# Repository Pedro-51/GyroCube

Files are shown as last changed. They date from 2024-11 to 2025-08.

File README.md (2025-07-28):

# GyroCube
 Self Balancing Cube Project

Balancing Cube project based on the "remrc" model: https://www.thingiverse.com/thing:6695891

    Creation of an Application to facilitate calibration and motor testing,
    Merging the main program with the motors test program,
    Creation of a printed circuit for those who wish to have a beautiful object,
    Addition of a Power button,
    Addition of a button to turn on the LEDs and change their colors,
    Modified the face files for placing the switches in 12 and 16mm. Thanks to dinomight.

Explanatory video: https://youtu.be/zuOgj580Nhk<br>
Led function video: https://youtu.be/vczHyelNjr4<br>
PCB: https://www.pcbway.com/project/shareproject/GyroCube_v1_1_5d583cf0.html<br>
Android app: [French](Appli%20APK/Cube_1_01_fr.apk),[English](Appli%20APK/Cube_1_01_en.apk)<br>

#######################################################################################

For the program to work, you need to install esp32 by expressif v2.0.17 board version

#######################################################################################

## 12-5-2024 (Dinomight/Darkmadda)
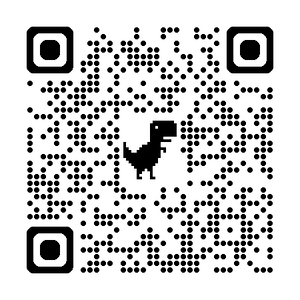
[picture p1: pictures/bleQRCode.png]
Added new [BLE firmware](esp32_cube_vBLE_en/) this has a browser based config tool (can be use on android/mac/pc via chrome). The firmware is written to be used with platformio rather than the arduino ide. it may still work the arduino ide but i'm not sure (Platformio is far superior anyways). This firmware is backwards compatible with other app config methods (Bluetooth Serial, Pedro android app). I however think the new BLE tool is superior. I'm a little biased but try it you'll see. no need to host the app i set it up on hosting that should never go away https://idoxa55.sufydely.com/cubeConfigTool.html.

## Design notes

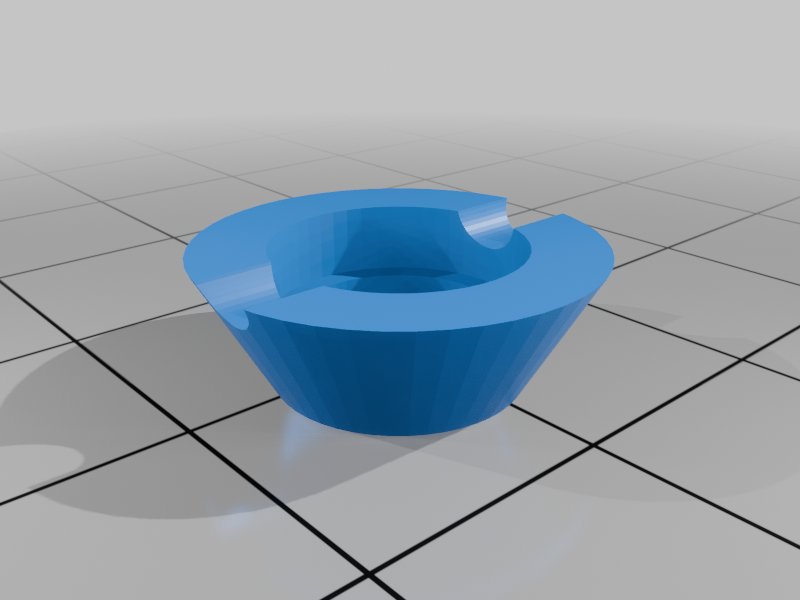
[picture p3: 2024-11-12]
3D_files/images/0f9c7aa1-d16f-406a-a5ba-5303668963a1.png

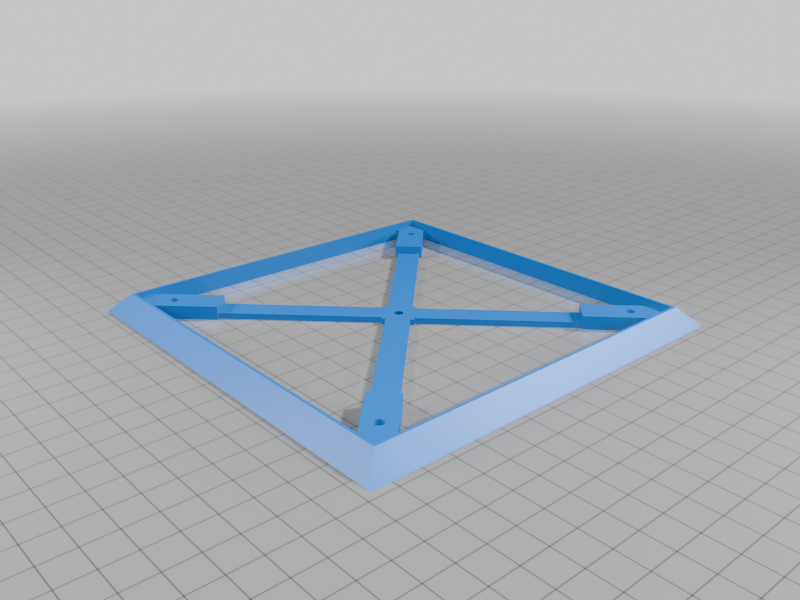
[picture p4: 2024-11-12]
3D_files/images/1357592c-b74b-4802-8180-4ac7882b1fb2.png

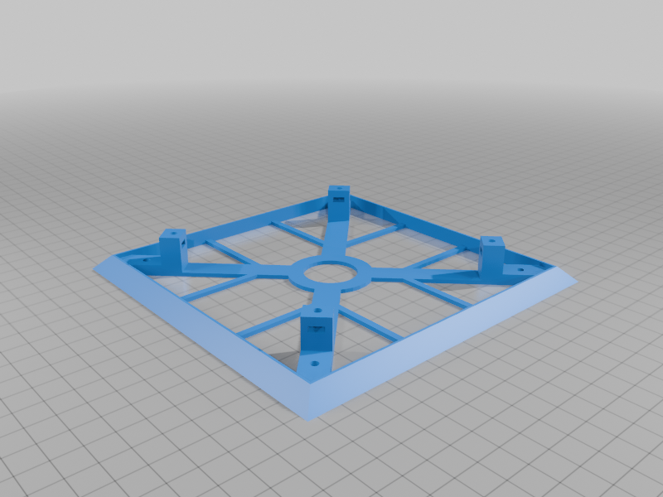
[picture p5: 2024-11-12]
3D_files/images/8a100be1-da8e-4f1d-b831-8e430dd452ee.png

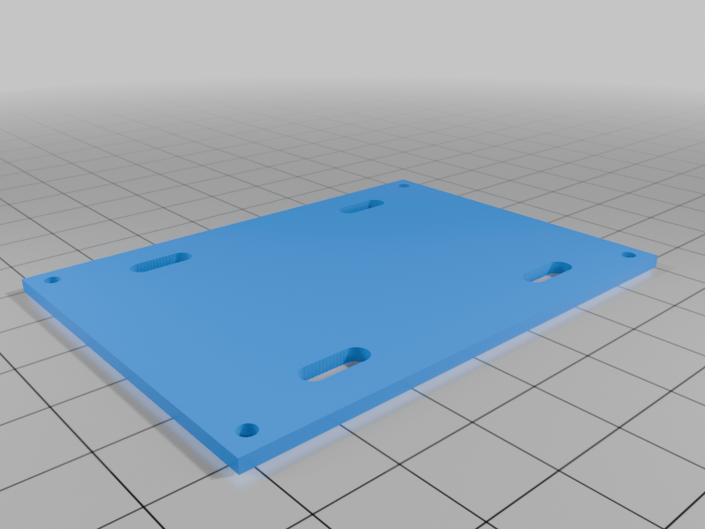
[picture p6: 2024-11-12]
3D_files/images/8ea0aab7-f794-4f8a-a906-e5200b60cf10.png

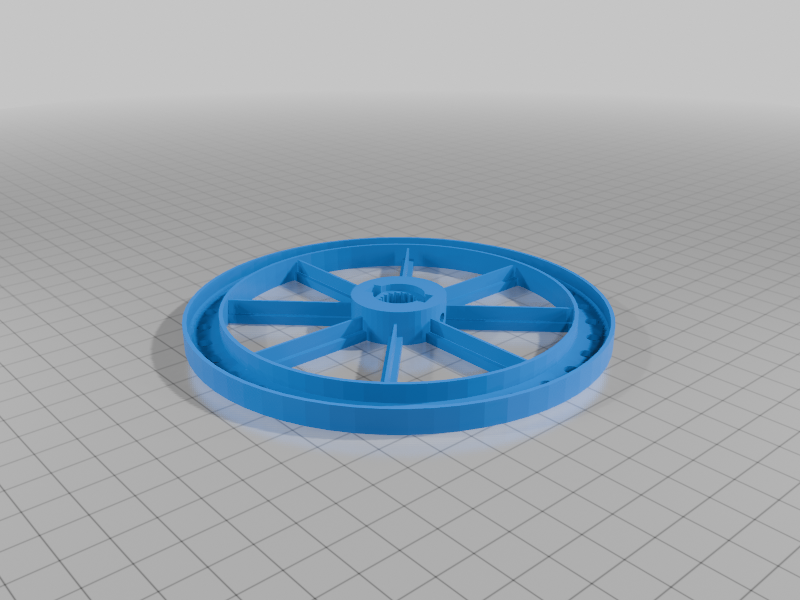
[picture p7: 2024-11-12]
3D_files/images/49ab8330-d06a-4846-8612-64cba1623243.png

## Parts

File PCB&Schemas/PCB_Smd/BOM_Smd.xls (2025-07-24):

Reference | Packages | Value | Qty | Comments
BT1 |  | Battery lipo 3s 650mah | 1
BZ1 |  | Buzzer 5v | 1
C1,C2 | 1206 SMD | 100nf | 2
J6,J7,J8 | JST-ZH 15cm | Connector jst-zh 01x08 double head | 3
J13 | JST-ZH 10cm | Connector jst-zh 01x03 with wire | 1
J12 | JST-ZH 10cm | Connector jst-zh 01x04 with wire | 1
Q1 | Sot-23-3 | MMBT2222A | 1
R1,R5 | 1206 SMD | 1k | 2
R2 | 1206 SMD | 33k | 1
R3,R4 | 1206 SMD | 10k | 2
SW1 | Ø16mm or Ø12mm 12-24v | Latch power inox switch | 1
SW2-1 | Ø16mm or Ø12mm 3-6v | Momentary inox switch | 1
SW2-2 |  | SMD switch reset Push | 1
U1 | mini360 | DC-DC 5v step down | 1
U2 | 30pin-micro module | esp32-wroom-32D cp2102 | 1
PCB | PCBway | PCB by Pedro51 | 1 | GyroCube_v1_2_Smd (https://www.pcbway.com/project/shareproject/GyroCube_v1_1_5d583cf0.html)
Wire | Silicon black wire | 16 AWG 100mm | 1
Wire | Silicon red wire | 16 AWG 100mm | 1
Wire | Silicon black wire | 24 AWG 100mm | 1
MPU6050 |  | Gyroscope | 1
WS1812 Led | Strip pcb for drone | Leds RGB PandaRC | 1
NIDEC 24H |  | Encoder Motor | 3
Battery Plug | Male | XT30 | 1
Screws | countersunk head screws | M4x8mm | 72
Screws | round head screw | M4x10mm | 12
Nuts | - | M4 | 144
Screws | countersunk head screws | M3x10mm | 36
Screws | countersunk head screws | M3x14mm | 12
Nuts | - | M3 | 52

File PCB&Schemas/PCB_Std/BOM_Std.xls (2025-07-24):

Reference | Packages | Value | Qty | Comments
BT1 |  | Battery lipo 3s 650mah | 1
BZ1 |  | Buzzer 5v | 1
C1,C2 | ceramic | 100nf-50v | 2
C3 | Polarized chimic | 100uf-10v | 1
J6,J7,J8 | JST-ZH 15cm | Connector jst-zh 01x08 double head | 3
J13 | JST-ZH 10cm | Connector jst-zh 01x03 with wire | 1
J12 | JST-ZH 10cm | Connector jst-zh 01x04 with wire | 1
Q1 | TO92 | 2n2222 | 1
R1,R5 | 1/4w | 1k | 2
R2 | 1/4w | 33k | 1
R3,R4 | 1/4w | 10k | 2
SW1 | Ø16mm or Ø12mm 12-24v | Latch power inox switch | 1
SW2-1 | Ø16mm or Ø12mm 3-6v | Momentary inox switch | 1
SW2-2 |  | switch reset Push | 1
U1 | TO220 | LM7805 DC-DC 5v regulator | 1
U2 | 30pin-micro module | esp32-wroom-32D cp2102 | 1
PCB | PCBway | PCB by Pedro51 | 1 | GyroCube_v1_2_Std (https://www.pcbway.com/project/shareproject/GyroCube_v1_2_Smd_9171484b.html)
Wire | Silicon black wire | 16 AWG 100mm | 1
Wire | Silicon red wire | 16 AWG 100mm | 1
Wire | Silicon black wire | 24 AWG 100mm | 1
MPU6050 |  | Gyroscope | 1
WS1812 Led | Strip pcb for drone | Leds RGB PandaRC | 1
NIDEC 24H |  | Encoder Motor | 3
Battery Plug | Male | XT30 | 1
Screws | countersunk head screws | M4x8mm | 72
Screws | round head screw | M4x10mm | 12
Nuts | - | M4 | 144
Screws | countersunk head screws | M3x10mm | 36
Screws | countersunk head screws | M3x14mm | 12
Nuts | - | M3 | 52

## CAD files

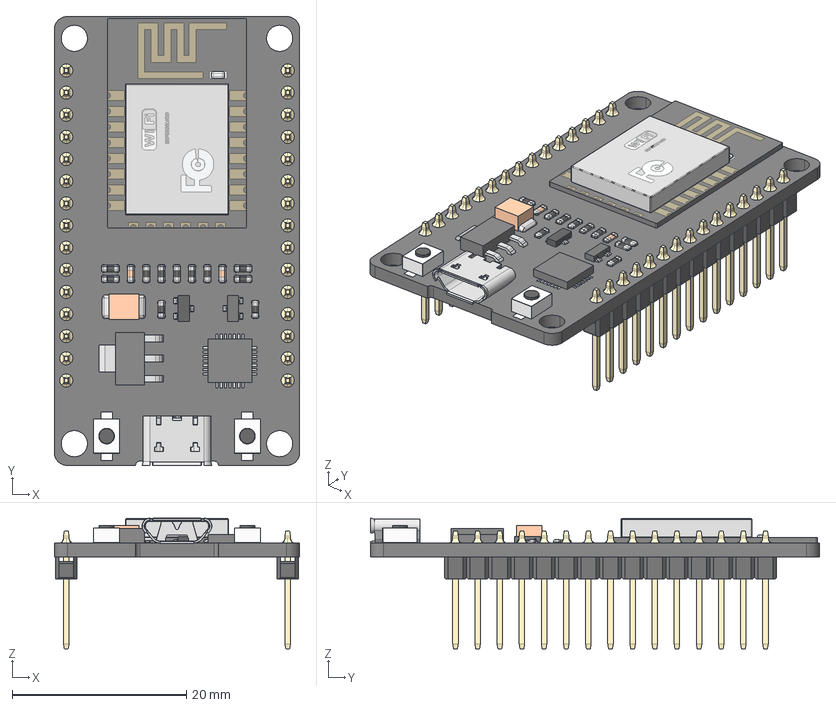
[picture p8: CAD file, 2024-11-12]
PCB&Schemas/PCB_Smd/Kidad_PCB_Smd/3d_Model/esp32_dev_kit_v1_asm.stp
28.1 x 51.5 x 15.0 mm
PCB
PIN x 30
WIFI_CARD_2
RECTANGULARCHIP_2
MICROCHIP_2
TANCHIP_2
TRANSISTOR_3-LEG_2
RESISTOR1_2 x 11
RESISTOR2-32_2 x 2
TRANSISTOR_3-LEG2_2
BUTTONFLASH-13_2 x 2
BUTTONFLASH-14_2 x 2
USB_SOCKET_2

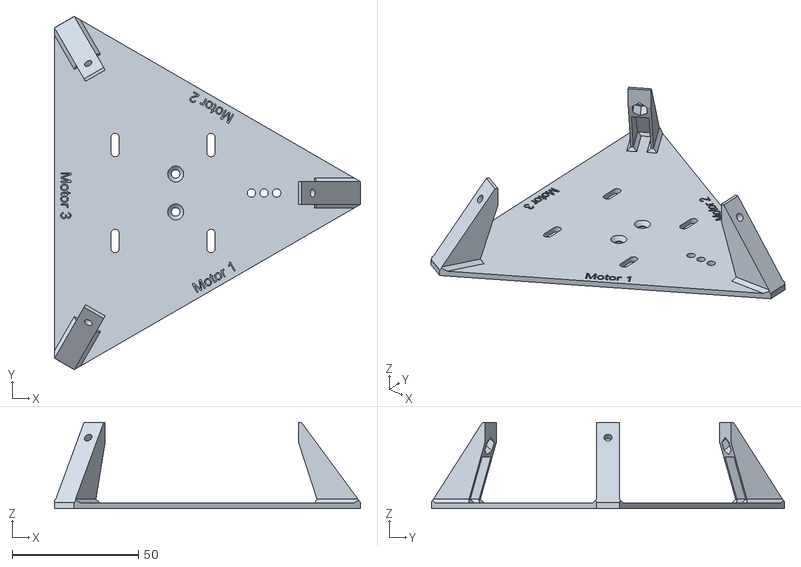
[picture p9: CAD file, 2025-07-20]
3D_files/cubli_midplate_v3_1x.stl
121.2 x 139.9 x 34.1

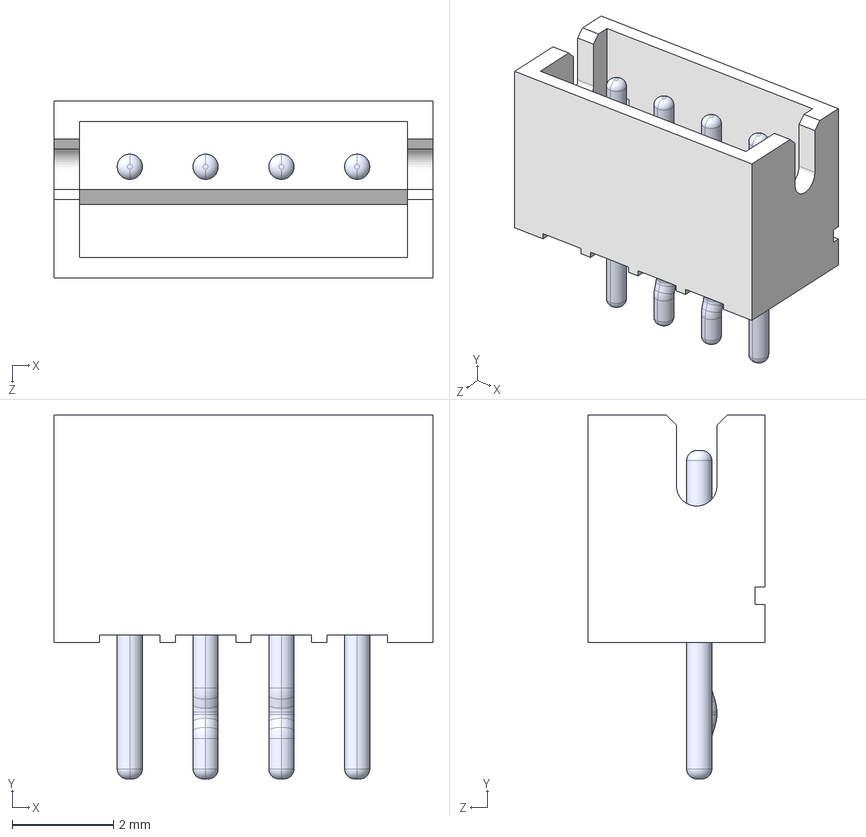
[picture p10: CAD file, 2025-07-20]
PCB&Schemas/PCB_Smd/Kidad_PCB_Smd/3d_Model/B4B-ZR--3DModel-STEP-56544.STEP
7.50 x 7.20 x 3.50 mm
BxB-ZR_4
pin_straight x 2
pin_Bent x 2

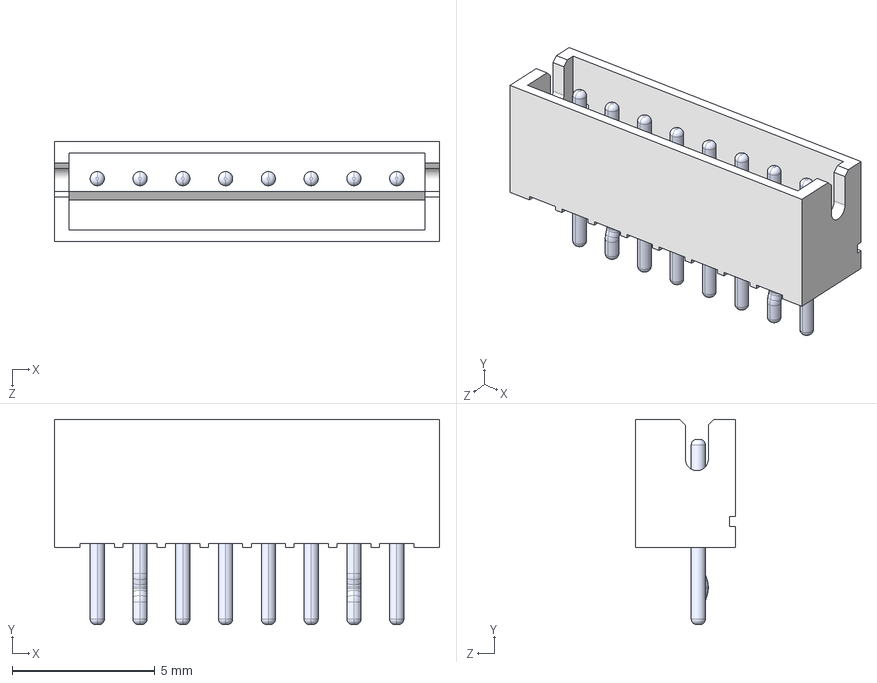
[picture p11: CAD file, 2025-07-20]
PCB&Schemas/PCB_Std/Kicad_PCB_Std/3d_Model/B8B-ZR -LF--SN---3DModel-STEP-56544.STEP
13.5 x 7.20 x 3.50 mm
BxB-ZR_8
pin_straight x 6
pin_Bent x 2

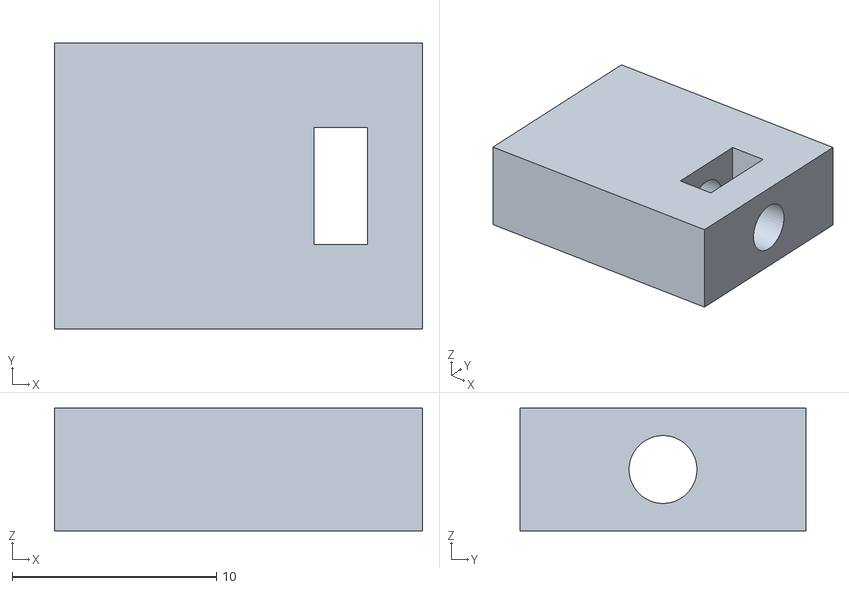
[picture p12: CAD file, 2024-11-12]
3D_files/cubli_battery_holder_2_1x.stl
18.0 x 14.0 x 6.00

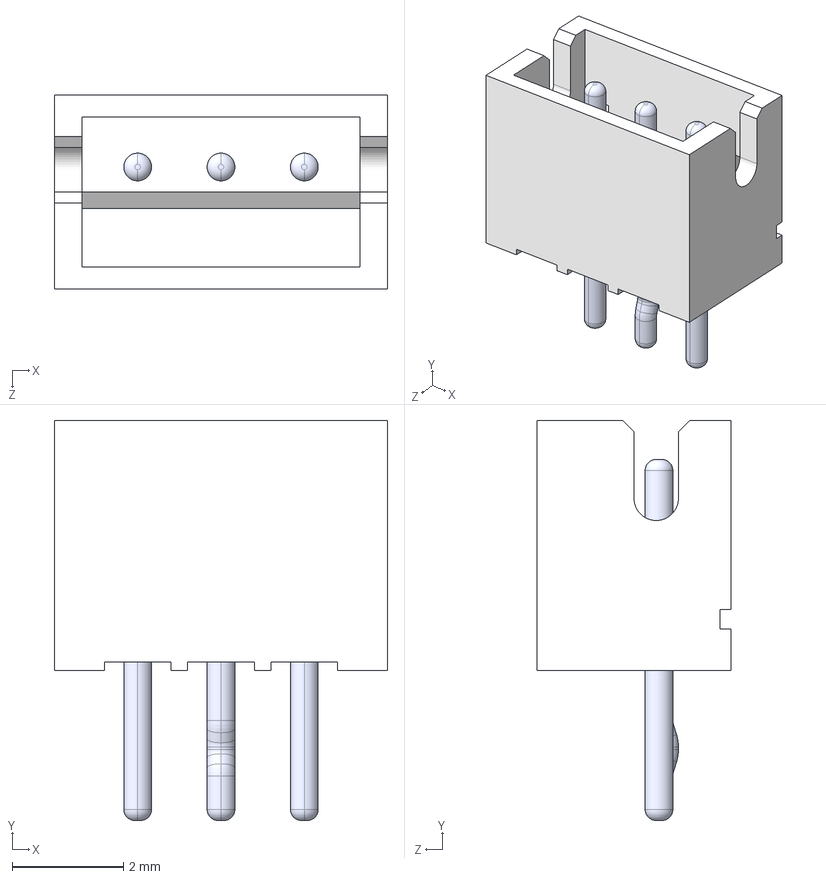
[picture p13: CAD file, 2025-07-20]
PCB&Schemas/PCB_Smd/Kidad_PCB_Smd/3d_Model/B3B-ZR--3DModel-STEP-56544.STEP
6.00 x 7.20 x 3.50 mm
BxB-ZR_3
pin_straight x 2
pin_Bent

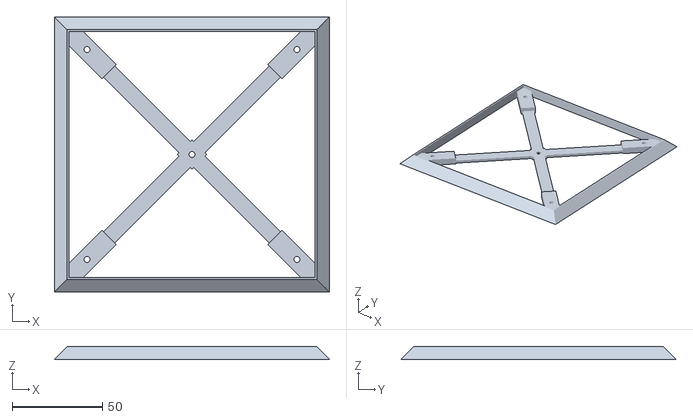
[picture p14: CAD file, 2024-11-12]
3D_files/cubli_side_std_1x.stl
152.0 x 152.0 x 7.00

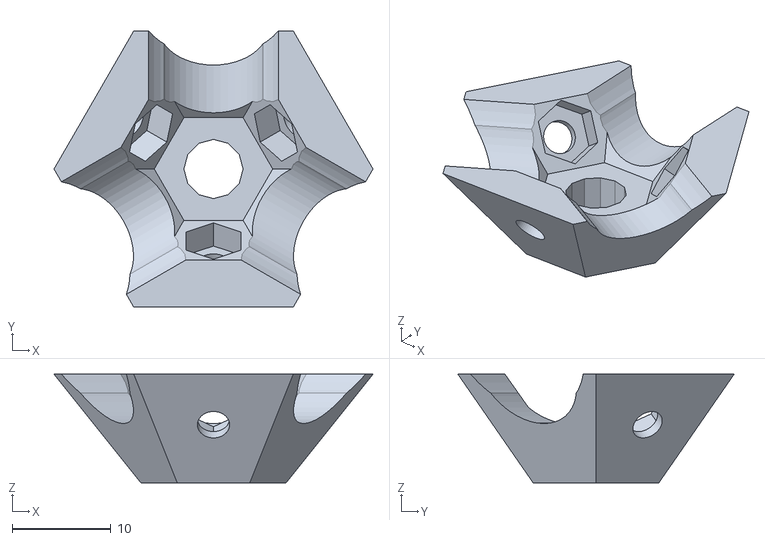
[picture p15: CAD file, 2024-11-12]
3D_files/cubli_corner_8x.stl
32.3 x 28.0 x 11.0

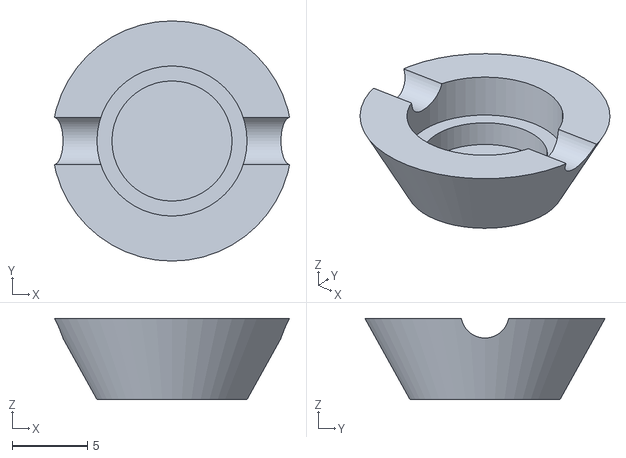
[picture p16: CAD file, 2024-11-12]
3D_files/cubli_led_cover_3x.stl
15.7 x 16.0 x 5.40

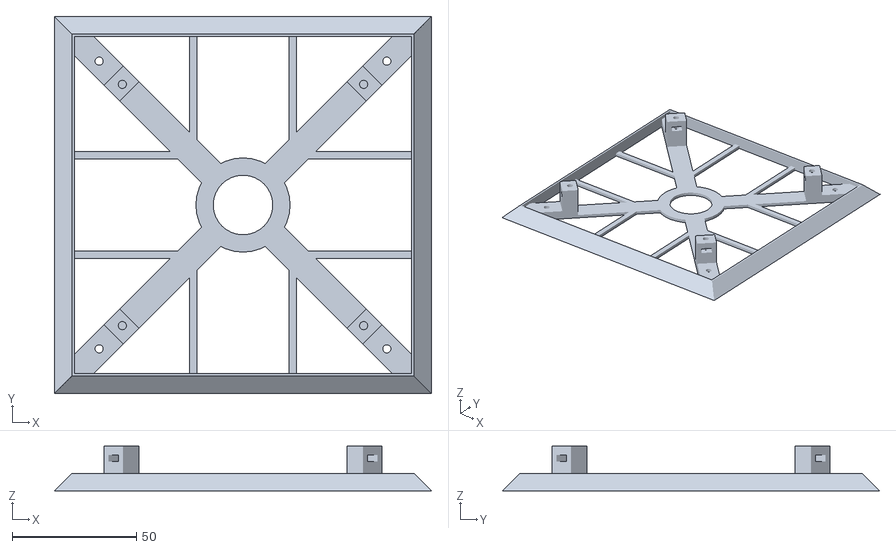
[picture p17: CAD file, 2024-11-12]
3D_files/cubli_rw_side_3x.stl
152.0 x 152.0 x 18.1

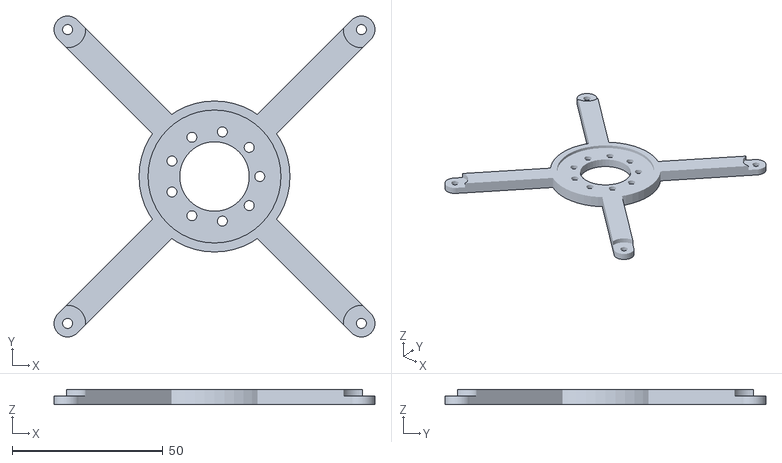
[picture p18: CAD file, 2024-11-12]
3D_files/cubli_motor_holder_3x.stl
106.3 x 106.3 x 5.00

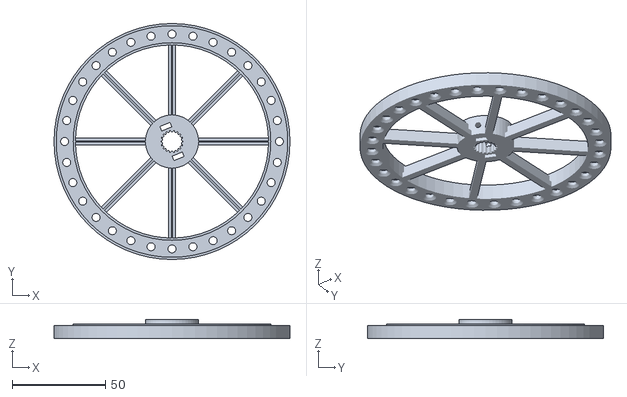
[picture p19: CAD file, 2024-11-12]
3D_files/cubli_reaction_wheel_3x.stl
126.4 x 126.4 x 10.4

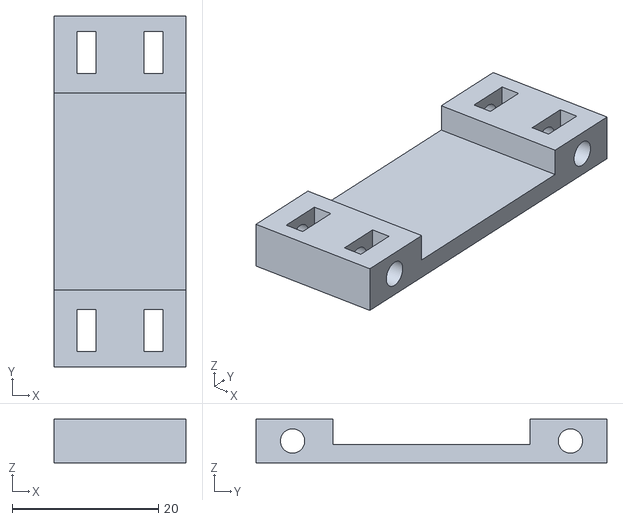
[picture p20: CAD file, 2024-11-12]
3D_files/cubli_battery_holder_1_2x.stl
18.0 x 48.0 x 6.00

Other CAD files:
3D_files/cubli_side_push_12mm.stl
3D_files/cubli_controller_holder_1x.stl
3D_files/cubli_side_push_16mm.stl

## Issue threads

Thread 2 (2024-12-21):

uint8_t requestFrom(int address, int size, int sendStop)

manuelchaves, 2024-12-21:
Windows 11, Arduino IDE V2.3.4, ESP32 V2.0.15 and ESP32-WROOM-DA module board.
when compiling I get this error uint8_t requestFrom(int address, int size, int sendStop) but the compilation is not aborted
Any tips?
Tks
[erro.txt](https://github.com/user-attachments/files/18220196/erro.txt)

Pedro-51, 2025-03-19:
Use esp32 board by expressif systems version 2.0.17

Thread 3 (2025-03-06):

Servo connections on PCB

mpaw, 2025-03-06:
What are the servo connections for? They are not mentioned anywhere in this repo aside from the PCB

mpaw, 2025-03-15:
@Pedro-51 Is there any documentation? I ordered the PCB and printed all the parts and am waiting on your response before assembling everything.

Pedro-51, 2025-03-19:
Hello, the servo jacks are not needed for this project.
Everything you need to know is in this GitHub repository. A video of the assembly will be coming soon.

mpaw, 2025-03-20:
@Pedro-51 Thanks for the response. I'm actually finishing putting together my cube now. Thanks for providing the PCB, everything came together really nice.

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

Closed 2025-07-28.

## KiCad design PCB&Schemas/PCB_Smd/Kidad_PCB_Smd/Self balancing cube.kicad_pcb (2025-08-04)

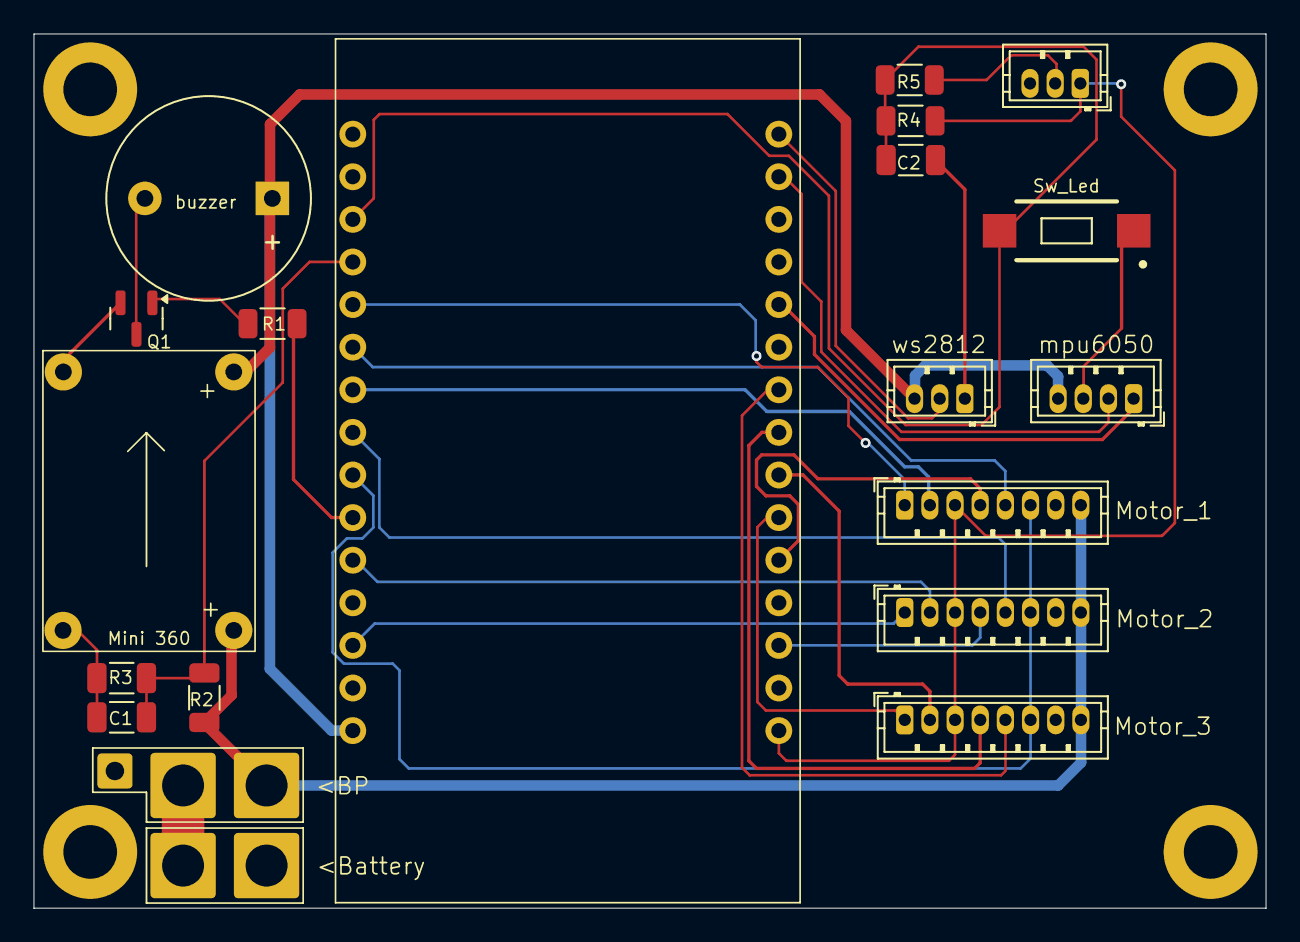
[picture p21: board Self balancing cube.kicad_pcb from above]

Board: 2 copper layers, 73.5 x 52.1 mm, 27 parts (0 on the bottom side), 27 nets.

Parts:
BZ1: Buzzer; Buzzer_12x9.5RM7.6
C1, C2: 100nf; C_1206_3216Metric
H1, H2, H3, H4: MountingHole; MountingHole_3.2mm_M3_DIN965_Pad
J1, J2, J3, J4: Conn_01x01; SolderWire-2sqmm_1x01_D2mm_OD3.9mm
J5: Conn_01x01; SolderWire-0.5sqmm_1x01_D0.9mm_OD2.1mm
J6, J7, J8: Conn_01x08_Pin; JST_ZH_B8B-ZR_1x08_P1.50mm_Vertical
J12: Conn_01x04_Pin; JST_ZH_B4B-ZR_1x04_P1.50mm_Vertical
J13, J14: Conn_01x03_Pin; JST_ZH_B3B-ZR_1x03_P1.50mm_Vertical
Q1: MMBT2222A; SOT-23
R1, R5: 1k; R_1206_3216Metric
R2: 33k; C_1206_3216Metric
R3: 10k; C_1206_3216Metric
R4: 10k; R_1206_3216Metric
SW2: SW_Push; SW_RS-032G05A3-SMRT
U1: 5v; DCDC buck
U2: esp module 30pins

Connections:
+3.3V: J6.3, J7.3, J8.3, J14.1, R4.2, U2.16 (3V3)
+5V: BZ1.1 (+), J12.4, J13.3, U1.3 (OUT+), U2.15 (VIN)
+BATT: J1.1, J6.8, J7.8, J8.8, R2.1, U1.1 (IN+)
-BATT: C1.2, C2.2, H1.1, H2.1, H3.1, H4.1, J4.1, J5.1, J6.7, J7.7, J8.7, J12.3, J13.1, J14.3, Q1.2 (E), R3.2, SW2.1, U1.2 (IN-), U1.4 (OUT-), U2.14 (GND)
Adc batt: C1.1, R2.2, R3.1, U2.4 (D34)
unnamed: BZ1.2 (-), Q1.3 (C)
unnamed: J2.1, J3.1
unnamed: J6.1, U2.5 (D35)
unnamed: J6.2, U2.7 (D33)
unnamed: J6.4, U2.20 (D4)
unnamed: J6.5, U2.6 (D32)
unnamed: J6.6, J7.6, J8.6, U2.9 (D26)
unnamed: J7.1, U2.13 (D13)
unnamed: J7.2, U2.11 (D14)
unnamed: J7.4, U2.18 (D15)
unnamed: J7.5, U2.8 (D25)
unnamed: J8.1, U2.21 (RX2)
unnamed: J8.2, U2.22 (TX2)
unnamed: J8.4, U2.23 (D5)
unnamed: J8.5, U2.24 (D18)
unnamed: J14.2, R5.1
unnamed: Q1.1 (B), R1.2
Push_Led: C2.1, R4.1, R5.2, SW2.2, U2.3 (VN)
SCL: J12.2, U2.29 (D22)
SDA: J12.1, U2.26 (D21)
WS2812: J13.2, U2.30 (D23)
cmd buzzer: R1.1, U2.10 (D27)

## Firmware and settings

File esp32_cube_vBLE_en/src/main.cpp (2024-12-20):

#include <MyCharacteristicCallbacks.h>
#include <MyServerCallbacks.h>
#include <ESP32.h>
#include <functions.h>
#include "BluetoothSerial.h"
#include <BLEDevice.h>
#include <BLEServer.h>
#include <BLEUtils.h>
#include <BLE2902.h>
#include <EEPROM.h>

/*
  Rui Santos & Sara Santos - Random Nerd Tutorials
  Complete project details at https://RandomNerdTutorials.com/esp32-web-bluetooth/
  Permission is hereby granted, free of charge, to any person obtaining a copy of this software and associated documentation files.
  The above copyright notice and this permission notice shall be included in all copies or substantial portions of the Software.
*/

BLEServer* pServer = NULL;
uint32_t value = 0;
TaskHandle_t Task1;
TaskHandle_t Task2;
BLECharacteristic* pSensorCharacteristic;
BLECharacteristic* pLedCharacteristic; 
float gyroX;
float gyroY;
float gyroZ;

float gyroYfilt;
float gyroZfilt;
float gyroXfilt;
word i;
int ledPin = 2; // Use the appropriate GPIO pin for your setup

// See the following for generating UUIDs:
// https://www.uuidgenerator.net/
#define SERVICE_UUID        "19b10000-e8f2-537e-4f6c-d104768a1214"
#define SENSOR_CHARACTERISTIC_UUID "19b10001-e8f2-537e-4f6c-d104768a1214"
#define COM_CHARACTERISTIC_UUID "19b10002-e8f2-537e-4f6c-d104768a1214"

bool play=false;

void setup() {
  Serial.begin(115200);    
  EEPROM.begin(EEPROM_SIZE);
  pinMode(ledPin, OUTPUT);
  // Create the BLE Device
  BLEDevice::init("Balance Cube");

  // Create the BLE Server
  pServer = BLEDevice::createServer();
  pServer->setCallbacks(new MyServerCallbacks());

  // Create the BLE Service
  BLEService *pService = pServer->createService(SERVICE_UUID);

  // Create a BLE Characteristic
  pSensorCharacteristic = pService->createCharacteristic(
                      SENSOR_CHARACTERISTIC_UUID,
                      BLECharacteristic::PROPERTY_READ   |
                      BLECharacteristic::PROPERTY_WRITE  |
                      BLECharacteristic::PROPERTY_NOTIFY |
                      BLECharacteristic::PROPERTY_INDICATE
                    );

  // Create the ON button Characteristic
  pLedCharacteristic = pService->createCharacteristic(
                      COM_CHARACTERISTIC_UUID,
                      BLECharacteristic::PROPERTY_WRITE
                    );
//   // Register the callback for the ON button characteristic
  pLedCharacteristic->setCallbacks(new MyCharacteristicCallbacks(testMotors, calibrate_edge, calibrate_vertex, getSettings, setSettings, saveSettings, setLeds, saveMotors));
  
  // https://www.bluetooth.com/specifications/gatt/viewer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
  // Create a BLE Descriptor
  pSensorCharacteristic->addDescriptor(new BLE2902());
  pLedCharacteristic->addDescriptor(new BLE2902());

  // Start the service
  pService->start();

  // Start advertising
  BLEAdvertising *pAdvertising = BLEDevice::getAdvertising();
  pAdvertising->addServiceUUID(SERVICE_UUID);
  pAdvertising->setScanResponse(false);
  pAdvertising->setMinPreferred(0x0);  // set value to 0x00 to not advertise this parameter
  BLEDevice::startAdvertising();
  Serial.println("Waiting a client connection to notify...");

  FastLED.addLeds<WS2812B, LED_PIN, RGB>(leds, NUM_PIXELS);  // GRB ordering is typical
  
  pinMode(BUZZER, OUTPUT);
  pinMode(BRAKE, OUTPUT);
  digitalWrite(BRAKE, HIGH);
  pinMode(INT_LED, INPUT);
  for (i=0;i<250;i+=10){ colorLed(i, i, 0, 1, 3, 5);}
  for (RGB_val=0;RGB_val<18;RGB_val++){
    Red = RGB_Color[RGB_val][0]; Green = RGB_Color[RGB_val][1]; Blue  = RGB_Color[RGB_val][2];
    colorLed(Red, Green, Blue, 1, 3, 80); //Red, Green, Blue, FirstPixel, LastPixel, Delay
  }
  for (i=250;i>0;i-=10){colorLed(i, i*0.68, 0, 1, 3, 5);}
  colorLed(0, 0, 0, 1, 3, 5);

  EEPROM.get(0, offsets);

  int m1=offsets.motor1;
  int m2=offsets.motor2;
  int m3=offsets.motor3;
  if(m1 < 0 || m1 > 3){
    m1=0;
    m2=1;
    m3=2;
    offsets.motor1 = 0;
    offsets.motor2 = 1;
    offsets.motor3 = 2;
    Serial.println("reseting pins");
    save();
  }
    Serial.println(m1);
    Serial.println(m2);
    Serial.println(m3);
  DIR1      = motors[m1][0];
  ENC1_1    = motors[m1][1];
  ENC1_2    = motors[m1][2];
  PWM1      = motors[m1][3];
  PWM1_CH   = motors[m1][4];

  DIR2      = motors[m2][0];
  ENC2_1    = motors[m2][1];
  ENC2_2    = motors[m2][2];
  PWM2      = motors[m2][3];
  PWM2_CH   = motors[m2][4];

  DIR3      = motors[m3][0];
  ENC3_1    = motors[m3][1];
  ENC3_2    = motors[m3][2];
  PWM3      = motors[m3][3];
  PWM3_CH   = motors[m3][4];

  pinMode(DIR1, OUTPUT);
  pinMode(ENC1_1, INPUT);
  pinMode(ENC1_2, INPUT);
  attachInterrupt(ENC1_1, ENC1_READ, CHANGE);
  attachInterrupt(ENC1_2, ENC1_READ, CHANGE);
  ledcSetup(PWM1_CH, BASE_FREQ, TIMER_BIT);
  ledcAttachPin(PWM1, PWM1_CH);
  Motor1_control(0);
  
  pinMode(DIR2, OUTPUT);
  pinMode(ENC2_1, INPUT);
  pinMode(ENC2_2, INPUT);
  attachInterrupt(ENC2_1, ENC2_READ, CHANGE);
  attachInterrupt(ENC2_2, ENC2_READ, CHANGE);
  ledcSetup(PWM2_CH, BASE_FREQ, TIMER_BIT);
  ledcAttachPin(PWM2, PWM2_CH);
  Motor2_control(0);
  
  pinMode(DIR3, OUTPUT);
  pinMode(ENC3_1, INPUT);
  pinMode(ENC3_2, INPUT);
  attachInterrupt(ENC3_1, ENC3_READ, CHANGE);
  attachInterrupt(ENC3_2, ENC3_READ, CHANGE);
  ledcSetup(PWM3_CH, BASE_FREQ, TIMER_BIT);
  ledcAttachPin(PWM3, PWM3_CH);
  Motor3_control(0);

  //offsets.ID = 0; // for debug
  if(offsets.ID == 255){
    offsets.ID = 0;
    offsets.Red = Red; offsets.Green = Green; offsets.Blue = Blue;
    offsets.edgeRed = edgeRed; offsets.edgeGreen = edgeGreen; offsets.edgeBlue = edgeBlue;
    offsets.vertexRed = vertexRed; offsets.vertexGreen = vertexGreen; offsets.vertexBlue = vertexBlue;
    offsets.K1 = K1; offsets.K2 = K2; offsets.K3 = K3; offsets.K4 = K4; offsets.zK2 = zK2; offsets.zK3 = zK3;
    offsets.eK1 = eK1; offsets.eK2 = eK2; offsets.eK3 = eK3; offsets.eK4 = eK4;
    save();
  }else if (offsets.ID == 96){
    Red = offsets.Red; Green = offsets.Green; Blue = offsets.Blue;
    vertexRed = offsets.vertexRed; vertexGreen = offsets.vertexGreen; vertexBlue = offsets.vertexBlue;
    edgeRed = offsets.edgeRed; edgeGreen = offsets.edgeGreen; edgeBlue = offsets.edgeBlue;
    K1 = offsets.K1; K2 = offsets.K2; K3 = offsets.K3; K4 = offsets.K4; zK2 = offsets.zK2; zK3 = offsets.zK3;
    eK1 = offsets.eK1; eK2 = offsets.eK2; eK3 = offsets.eK3; eK4 = offsets.eK4;
    calibrated = true;
  }
play=false;
  angle_setup();
  // xTaskCreatePinnedToCore (
  //   musicLoop,     // Function to implement the task
  //   "musicLoop",   // Name of the task
  //   10000,      // Stack size in bytes
  //   NULL,      // Task input parameter
  //   0,         // Priority of the task
  //   &Task1,      // Task handle.
  //   0          // Core where the task should run
  // );
}

void loop() {
  // disconnecting
  if (!deviceConnected && oldDeviceConnected) {
    Serial.println("Device disconnected.");
    delay(500); // give the bluetooth stack the chance to get things ready
    pServer->startAdvertising(); // restart advertising
    Serial.println("Start advertising");
    oldDeviceConnected = deviceConnected;
  }
  // connecting
  if (deviceConnected && !oldDeviceConnected) {
    // do stuff here on connecting
    oldDeviceConnected = deviceConnected;
            pSensorCharacteristic->setValue("");
            pSensorCharacteristic->notify();
            lasttime = millis();
    Serial.println("Device Connected");
  }
  currentT = millis();
  if (currentT - previousT_1 >= loop_time) {
    Tuning();
    angle_calc();
        
    motor1_speed = enc_count1;
    enc_count1 = 0;
    motor2_speed = enc_count2;
    enc_count2 = 0;
    motor3_speed = enc_count3;
    enc_count3 = 0;
    

  if (Mode == 0){

    threeWay_to_XY(motor1_speed, motor2_speed, motor3_speed);
    motors_speed_Z = motor1_speed + motor2_speed + motor3_speed;
    
    if (vertical_vertex && calibrated && !calibrating) {    
      digitalWrite(BRAKE, HIGH);
      gyroX = GyX / 131.0;
      gyroY = GyY / 131.0;
      gyroZ = GyZ / 131.0;
      gyroXfilt = alpha * gyroX + (1 - alpha) * gyroXfilt;
      gyroYfilt = alpha * gyroY + (1 - alpha) * gyroYfilt;
      
      int pwm_X = constrain(K1 * robot_angleX + K2 * gyroXfilt + K3 * speed_X + K4 * motors_speed_X, -255, 255);
      int pwm_Y = constrain(K1 * robot_angleY + K2 * gyroYfilt + K3 * speed_Y + K4 * motors_speed_Y, -255, 255);
      int pwm_Z = constrain(zK2 * gyroZ + zK3 * motors_speed_Z, -255, 255);

      motors_speed_X += speed_X / 5; 
      motors_speed_Y += speed_Y / 5;
      XYZ_to_threeWay(-pwm_X, pwm_Y, -pwm_Z);
      balancing("Vertex");
      colorLed(vertexRed, vertexGreen, vertexBlue, 1, 3, 0); 
    } else if (vertical_edge && calibrated && !calibrating) {
      digitalWrite(BRAKE, HIGH);
      gyroX = GyX / 131.0;
      gyroXfilt = alpha * gyroX + (1 - alpha) * gyroXfilt;
      
      int pwm_X = constrain(eK1 * robot_angleX + eK2 * gyroXfilt + eK3 * motor3_speed + eK4 * motors_speed_X, -255, 255);
      
      motors_speed_X += motor3_speed / 5;
      Motor3_control(pwm_X);
      balancing("Edge");
      colorLed(edgeRed, edgeGreen, edgeBlue, 1, 3, 0); 
    } else {
      XYZ_to_threeWay(0, 0, 0);
      digitalWrite(BRAKE, LOW);
      motors_speed_X = 0;
      motors_speed_Y = 0; 
      colorLed(0, 0, 0, 1, 3, 0); 
      if  (!calibrating and calibrated) {
        RGB_Process();
      }
    }
  }

  if (Mode == 1 ){
      switch (f) {
        case 1:
          digitalWrite(BRAKE, HIGH);
          if(lock){
            Serial.println("Rotating motor 1.");
            SerialBT.println("46");
            pSensorCharacteristic->setValue(String("*m1*Rotating").c_str());
            pSensorCharacteristic->notify();
          }
          Motor1_control(50);
          break;
        case 4:
          digitalWrite(BRAKE, LOW);
          if(lock){
            Serial.println("Stop.");
            SerialBT.println("41");
            pSensorCharacteristic->setValue(String("*m1*Stop").c_str());
            pSensorCharacteristic->notify();
          }
          Motor1_control(0);
          break;      
        case 7:
          digitalWrite(BRAKE, HIGH);
          if(lock){
            Serial.println("Change direction..."); SerialBT.println("42");
            pSensorCharacteristic->setValue(String("*m1*Reversing.").c_str());
            pSensorCharacteristic->notify();
          }
          Motor1_control(-50);
          break;
        case 10:
          digitalWrite(BRAKE, LOW); 
          if(lock){
            Serial.println("Stop."); 
            SerialBT.println("41");
            pSensorCharacteristic->setValue(String("*m1*Stop").c_str());
            pSensorCharacteristic->notify();
          }
          Motor1_control(0);
          break; 
        case 13:
          digitalWrite(BRAKE, HIGH);
          if(lock){
            Serial.println("Checking encoder...");
            SerialBT.println("43");
            pSensorCharacteristic->setValue(String("*m1*Checking encoder.").c_str());
            pSensorCharacteristic->notify();
          }
          Motor1_control(70);
          break; 
        case 16:
          digitalWrite(BRAKE, LOW);
          if (lock && motor1_speed > 300) {
            Serial.println("Encoder OK."); 
            Serial.print("Speed: "); Serial.println(motor1_speed);
            char str[22];
            sprintf(str, "*m1*Speed: %u", motor1_speed);
            pSensorCharacteristic->setValue(str);
            pSensorCharacteristic->notify();
          Motor1_control(70);

            s1.concat(motor1_speed);
            SerialBT.println("44"  + s1);
            Serial.println("Stop.");
          } else if (lock && motor1_speed <= 0) {
            Serial.println("Encoder FAIL.");
            Serial.print("Speed: "); Serial.println(motor1_speed);
              char str[22];
              pSensorCharacteristic->setValue(String("*m1*Encoder Fail").c_str());
              pSensorCharacteristic->notify();
            s1.concat(motor1_speed);
            SerialBT.println("45"  + s1);
            Serial.println("Stop.");
          }
          s1 = "";
          Motor1_control(0);
          break;      
  
        case 19:
          digitalWrite(BRAKE, HIGH);
          if(lock){
            Serial.println("Rotating motor 2."); SerialBT.println("47");
            pSensorCharacteristic->setValue(String("*m2*Rotating.").c_str());
            pSensorCharacteristic->notify();
          }
          Motor2_control(50);
          break;
        case 22:
          digitalWrite(BRAKE, LOW);
          if(lock){
            Serial.println("Stop."); 
            SerialBT.println("41");
            pSensorCharacteristic->setValue(String("*m2*Stop").c_str());
            pSensorCharacteristic->notify();
          }
          Motor2_control(0);
          break;      
        case 25:
          digitalWrite(BRAKE, HIGH);
          if (lock) {
            Serial.println("Change direction..."); 
            SerialBT.println("42");
            pSensorCharacteristic->setValue(String("*m2*Reversing.").c_str());
            pSensorCharacteristic->notify();
          }
          Motor2_control(-50);
          break;
        case 28:
          digitalWrite(BRAKE, LOW);
          if (lock) {
            Serial.println("Stop."); 
            SerialBT.println("41");
            pSensorCharacteristic->setValue(String("*m2*Stop").c_str());
            pSensorCharacteristic->notify();
          }
          Motor2_control(0);
          break; 
        case 31:
          digitalWrite(BRAKE, HIGH);
          if (lock) {
            Serial.println("Checking encoder..."); 
            SerialBT.println("43");
            pSensorCharacteristic->setValue(String("*m2*Checking encoder.").c_str());
            pSensorCharacteristic->notify();
          }
        Motor2_control(70);
          break; 
        case 34:
          digitalWrite(BRAKE, LOW);
          if (lock && motor2_speed > 300) {
            Serial.println("Encoder OK.");
            Serial.print("Speed: "); Serial.println(motor2_speed);
            s1.concat(motor2_speed);

            char str[22];
            sprintf(str, "*m2*Speed: %u", motor2_speed);
            pSensorCharacteristic->setValue(str);
            pSensorCharacteristic->notify();
            SerialBT.println("44"  + s1);
            Serial.println("Stop.");
          } else if (lock && motor2_speed <= 0) {
            Serial.println("Encoder FAIL.");
            Serial.print("Speed: "); Serial.println(motor2_speed);
            pSensorCharacteristic->setValue("*m2*Encoder Fail");
            pSensorCharacteristic->notify();
            s1.concat(motor2_speed);
            SerialBT.println("45"  + s1);
            Serial.println("Stop.");
          }
          s1 = "";
          Motor2_control(0);
          break;        
  
        case 37:
          digitalWrite(BRAKE, HIGH);
          if (lock) {
            Serial.println("Rotating motor 3."); 
            SerialBT.println("48");
            pSensorCharacteristic->setValue(String("*m3*Rotating.").c_str());
            pSensorCharacteristic->notify();
          }
          Motor3_control(50);
          break;
        case 40:
          digitalWrite(BRAKE, LOW);
          if (lock) {
            Serial.println("Stop."); 
            SerialBT.println("41");
            pSensorCharacteristic->setValue(String("*m3*Stop").c_str());
            pSensorCharacteristic->notify();
          }
          lock = 0;
          Motor3_control(0);
          break;      
        case 43:
          digitalWrite(BRAKE, HIGH);
          if (lock) {
            Serial.println("Change direction..."); 
            SerialBT.println("42");
            pSensorCharacteristic->setValue(String("*m3*Reversing.").c_str());
            pSensorCharacteristic->notify();
          }
          Motor3_control(-50);
          break;
        case 46:
          digitalWrite(BRAKE, LOW);
          if (lock) {
            Serial.println("Stop."); 
            SerialBT.println("41");
            pSensorCharacteristic->setValue(String("*m3*Stop").c_str());
            pSensorCharacteristic->notify();
          }
          Motor3_control(0);
          break; 
        case 49:
          digitalWrite(BRAKE, HIGH);
          if (lock) {
            Serial.println("Checking encoder..."); 
            SerialBT.println("43");
            pSensorCharacteristic->setValue(String("*m3*Checking Encoder").c_str());
            pSensorCharacteristic->notify();
          }
          Motor3_control(70);
          break; 
        case 52:
          digitalWrite(BRAKE, LOW);
          if (lock && motor3_speed > 300) {
            Serial.println("Encoder OK.");
            Serial.print("Speed: "); Serial.println(motor3_speed);
            s1.concat(motor3_speed);
            char str[22];
            sprintf(str, "*m3*Speed: %u", motor3_speed);
            pSensorCharacteristic->setValue(str);
            pSensorCharacteristic->notify();
            SerialBT.println("44"  + s1);
            Serial.println("Stop.");
          } else if (lock && motor3_speed <= 0) {
            Serial.println("Encoder FAIL.");
            Serial.print("Speed: "); 
            Serial.println(motor3_speed);
            pSensorCharacteristic->setValue("*m3*Encoder Fail");
            pSensorCharacteristic->notify();
            s1.concat(motor3_speed);
            SerialBT.println("45"  + s1);
            Serial.println("Stop.");
          }
          s1 = "";
          Motor3_control(0);
          break;        
        }
        lock = 0;
  }
    
  previousT_1 = currentT;
}    
  if (currentT - previousT_2 >= 1000) {

    battVoltage((double)analogRead(VBAT) / 204); // value 204 must be selected by measuring battery voltage!
    
    if (!calibrated && !calibrating) {
      Serial.println("first you need to calibrate the balancing points...");
      SerialBT.println("95");

      //pSensorCharacteristic->setValue("*a*First you need to calibrate the balancing points...");
      //pSensorCharacteristic->notify();
      if (!calibrated_leds) {
        colorLed(0, 50, 0, 1, 3, 0); 
        calibrated_leds = true; 
      } else {
        colorLed(0, 0, 0, 1, 3, 0); 
        calibrated_leds = false; 
      }
    }
    
    if (Mode == 1){
      f++; 
      if (f == 53){ beep(); Serial.println("End of Engine Tests."); SerialBT.println("96"); f = 1; Mode = 0;} 
    lock = 1;
    }
    previousT_2 = currentT;
  }
  
  if (ConnectBT == true && (currentT - previousT_3) > DelayBT)
      {
        init_BT();
        ConnectBT = false;
      }
}

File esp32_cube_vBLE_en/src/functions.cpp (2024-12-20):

#include <Arduino.h>
#include "functions.h"
#include <Wire.h>
#include <EEPROM.h>
BluetoothSerial SerialBT;
CRGB leds[NUM_PIXELS];
byte Mode, j, RGB_val;
bool LedRGB, Push, ChooseColor;
float speed_X, speed_Y;
OffsetsObj offsets;
int16_t motor1_speed, motor2_speed, motor3_speed;
int16_t AcX;
int16_t AcY;
int16_t AcZ;
int16_t AcXc;
int16_t AcYc;
int16_t AcZc;
int16_t GyX;
int16_t GyY;
int16_t GyZ;
float robot_angleX;
float robot_angleY;
float Acc_angleX; 
float Acc_angleY;  
long currentT;
long previousT_1;
long previousT_2;
long previousT_3;
byte f;
bool lock;
long lasttime;
long batterylasttime = millis();
int32_t motors_speed_X; 
int32_t motors_speed_Y; 
int32_t motors_speed_Z;
bool balanceNotify = true;
int DIR1;
int ENC1_1;
int ENC1_2;
int PWM1;
int PWM1_CH;

int DIR2;
int ENC2_1;
int ENC2_2;
int PWM2;
int PWM2_CH;

int DIR3;
int ENC3_1;
int ENC3_2;
int PWM3;
int PWM3_CH;
int melody[] = {
    NOTE_G5,4,
    NOTE_C6,4,
    NOTE_B5,4,
    NOTE_AS5,8,
    NOTE_B5,8,
    NOTE_AS5,8,
    // ----
    NOTE_A5,8,
    NOTE_GS5,4,
    NOTE_G5,4,
    NOTE_FS5,4,
    // ----
    NOTE_G5,4,
    NOTE_A5,4,
    NOTE_GS5,4,
    NOTE_G5,8,
    NOTE_GS5,8,
    NOTE_G5,8,
    // ----
    NOTE_FS5,8,
    NOTE_F5,4,
    NOTE_E5,4,
    NOTE_DS5,4,
    // ----
    NOTE_E5,4,
    NOTE_G5,8,
    NOTE_F5,8,
    NOTE_F5,4,
    NOTE_CS5,4,
    // ----
    NOTE_D5,4,
    NOTE_G5,8,
    NOTE_F5,8,
    NOTE_F5,4,
    NOTE_CS5,4,
    // ----
    NOTE_D5,4,
    NOTE_B4,8,
    NOTE_C5,8,
    NOTE_CS5,8,
    NOTE_D5,8,
    NOTE_DS5,8,
    NOTE_E5,8,
    NOTE_F5,8,
    // -----
    NOTE_FS5,8,
    NOTE_G5,8,
    NOTE_GS5,8,
    NOTE_A5,8,
    NOTE_B5,8,
    NOTE_A5,4,
    NOTE_G5,4,
    // -----
  };
void writeTo(byte device, byte address, byte value) {
  Wire.beginTransmission(device);
  Wire.write(address);
  Wire.write(value);
  Wire.endTransmission(true);
}

void beep() {
    digitalWrite(BUZZER, HIGH);
    delay(2);
    digitalWrite(BUZZER, LOW);
    delay(80);
}
    
//***********************************************************************
// Initialise Bluetooth
//***********************************************************************
void init_BT()
{
        Mode = 0; loop_time = 15;
        calibrating = false;
        colorLed(0, 0, 0, 1, 3, 0);
        LedRGB = false;
}

//***********************************************************************
// Rgb Led Command
//***********************************************************************
void colorLed(int Red, int Green, int Blue , int firstled, int lastled, int wait) {
    for(int i = firstled-1; i < lastled; i++) {    // For each pixel in strip...
    leds[i] = CRGB(Red, Green, Blue);
    FastLED.show();                          //  Update strip to match
  }
    delay(wait);                           //  Pause for a moment
}

//***********************************************************************
// Rgb Led Process
//***********************************************************************
void RGB_Process(){
  j = 0;
  while (digitalRead(INT_LED) == LOW){
    if (Push == false){Push = true;}
    j++; delay (5);
    if (j >= 250){break;}
  }
  if (!ChooseColor){
    if (Push == true){
      if (j < 250){
        if (LedRGB == true){
          colorLed(0, 0, 0, 1, 3, 0);
          LedRGB = false;
        }else{
          colorLed(Red, Green, Blue, 1, 3, 0);
          LedRGB = true;
        }
        beep();
      }else{
        j = 0; Push = false; LedRGB = true; 
        colorLed(Red, Green, Blue, 1, 3, 80);
        colorLed(0, 0, 0, 1, 3, 80);
        colorLed(Red, Green, Blue, 1, 3, 0); beep ();
        while (digitalRead(INT_LED) == LOW){}
        delay (5); ChooseColor = true;
      }
    }
  }else{
    if (Push == true){
      if (j < 250){
        if (RGB_val < 18){RGB_val++;}else{RGB_val = 0;}
        Red = RGB_Color[RGB_val][0]; Green = RGB_Color[RGB_val][1]; Blue = RGB_Color[RGB_val][2];
        colorLed(Red, Green, Blue, 1, 3, 0);
        Push = false; j = 0;
        beep();
      }else{
        offsets.Red = Red; offsets.Green = Green; offsets.Blue = Blue; offsets.ID = 96;
        save();
        colorLed(0, 0, 0, 1, 3, 0); 
        beep (); colorLed(Red, Green, Blue, 1, 3, 0); 
        beep ();
        Push = false; ChooseColor = false;
      }
    }
  }
  while (digitalRead(INT_LED) == LOW){}
  if (Push == true){Push = false;}
  delay (5);
}

void save() {
    EEPROM.put(0, offsets);
    EEPROM.commit();
    beep();
}

void angle_setup() {
  Wire.begin();
  delay (100);
  writeTo(MPU6050, PWR_MGMT_1, 0);
  writeTo(MPU6050, ACCEL_CONFIG, accSens << 3); // Specifying output scaling of accelerometer
  writeTo(MPU6050, GYRO_CONFIG, gyroSens << 3); // Specifying output scaling of gyroscope
  delay (100);
  
  beep();
  colorLed(50, 0, 0, 3, 3, 0);
  for (int i = 0; i < 512; i++) {
    angle_calc();
    GyZ_offset_sum += GyZ;
    delay(5);
  }
  GyZ_offset = GyZ_offset_sum >> 9;
  Serial.print("GyZ offset value = "); Serial.println(GyZ_offset);
  beep();
  colorLed(0, 0, 0, 3, 3, 0);

  colorLed(50, 0, 0, 2, 2, 0);
  for (int i = 0; i < 512; i++) {
    angle_calc();
    GyY_offset_sum += GyY;
    delay(5);
  }
  GyY_offset = GyY_offset_sum >> 9;
  Serial.print("GyY offset value = "); Serial.println(GyY_offset);
  beep();
  colorLed(0, 0, 0, 2, 2, 0);

  colorLed(50, 0, 0, 1, 1, 0);
  for (int i = 0; i < 512; i++) {
    angle_calc();
    GyX_offset_sum += GyX;
    delay(5);
  }
  GyX_offset = GyX_offset_sum >> 9;
  Serial.print("GyX offset value = "); Serial.println(GyX_offset);
  colorLed(50, 0, 0, 1, 1, 150);
  beep();
  beep();
  colorLed(50, 0, 0, 1, 3, 300);
  colorLed(0, 0, 0, 1, 3, 150);
  colorLed(50, 0, 0, 1, 3, 300);
  colorLed(0, 0, 0, 1, 3, 0);
}
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

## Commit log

2024-11-12 Version 1.10
    [BOM.xls, Self balancing cube.kicad_pcb, Self balancing cube.kicad_sch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]
2024-12-05 adding link to pcbway
2024-12-06 v1.0 firmware. adding version checking, and motor remapping
2024-12-06 don't track .DS_Store files
2024-12-07 adding led colors to web interface, fixing motor testing progress
2025-02-14 Version 1.11
    Added schematic to facilitate assembly, modified program to check if motors are properly connected to the board.
    [Self balancing cube.kicad_pcb, Self balancing cube.kicad_sch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]
2025-02-14 Update BOM
    [BOM.xls]
2025-02-14 Version 1.11
    Update
    [BOM.xls]
2025-07-20 Version 1.13
    Modified the printed circuit board and created a PCB for through-hole components.
    Bug fixes in the program.
    [B3B-ZR--3DModel-STEP-56544.STEP, B4B-ZR--3DModel-STEP-56544.STEP, B8B-ZR -LF--SN---3DModel-STEP-56544.STEP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]
2025-07-24 Version 1.13.1
    [B3B-ZR--3DModel-STEP-56544.STEP, B4B-ZR--3DModel-STEP-56544.STEP, B8B-ZR -LF--SN---3DModel-STEP-56544.STEP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]
2025-08-04 Correction PCB
    [Self balancing cube-B_Cu.gbr, Self balancing cube-B_Mask.gbr, Self balancing cube-B_Silkscreen.gbr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]

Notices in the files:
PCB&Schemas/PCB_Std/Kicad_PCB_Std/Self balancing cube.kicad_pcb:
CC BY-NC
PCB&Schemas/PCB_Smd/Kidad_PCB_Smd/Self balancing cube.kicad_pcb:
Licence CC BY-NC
